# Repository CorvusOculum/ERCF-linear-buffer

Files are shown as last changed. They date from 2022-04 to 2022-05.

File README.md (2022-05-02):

# ERCF-linear-buffer

NOTE: This is a work in progress.

This is a filament buffer system designed to replace the "caged loops" style of buffer that is popular, such as the Enraged Rabbit Carrot Patch.  This buffer differs from caged loops in that the filament is pushed down a very long linear channel as a single loop.  The narrow, yet wide channel prevents the filament from twisting.  When a particular channel is in use, the filament is retracted out of the channel and only contacts half of the pulley leading to very little drag in the system.  The channels are cut from 3/8 inch thick foam board.

I designed this system as a low drag alternative to the Carrot Patch style of buffer which can in my own experience be problematice with very long reverse-bowden lengths.  With a looping system, you add loops to add distance to the buffer.  When you add four or five loops, the drag can be quite significant.  This system only ever has a half loop of the pulley and when more length is needed, you simply use longer channels.  

# BOM

(N refers to the number of channels in your MMU system) 

    xN - Buffer Channel Pulley Block
    
    xN - Buffer Channel Top Block
    
    xN - Buffer Channel Pulley
    
    xN - Buffer Channel Pulley Axel
    
    xN - Buffer Channel Bottom Block
    
    xN - Buffer Channel Desiccant Tray
    
    xN - 608 RS "Skateboard" Bearing
         NOTE: I personally remove the seals with a sharp tool, and 
         then use a cleaner such as break cleaner to completely remove 
         all grease from the bearing.  The pulleys should spin like a
         fidget spinner when completed.  I don't know if this helps 
         anything at all...  But I do it anyway...
    
    2 x N / 3 - Buffer Channel Brace Bracket
         NOTE: You will want a 2 braces per channel to support the 
         foam board and mount the buffers to whatever you'll be using. 
         So in a 9 channel MMU system you will want: 2*9/3= 6 Brackets. 
    
    xN - M3 x 35mm SHCS
    xN - M3 Heatset Inserts
    
    28 x N - 6mm x 3mm disc magnets 
          NOTE: Depending on the quality of your magnets you may be able
          to use fewer.  The parts are designed to accomodate a lot of 
          magnets on the assumption that you will be using cheap ones from
          AliExpress or Amazon.  If you have genuine N52's for example, far
          fewer will be required.  Experiment.
    
    2 x N - PC4-M10 Straight through Pneumatic Fitting
	      NOTE: MUST BE A THROUGH FITTING!

# Printing

While I printed mine in ABS with the standard Voron recomended profile, you could certainly dial down infill and perimeters and still be fine...  The buffers will not experience very much if any mechanical stress.  

# Construction

Your foam board should be cut using calipers.  Measure the inside of the narrow side of the channel and lock the calipers off.  Then use the calipers to score the foamboad.  Cut carefully with a long metal straightedge.  Do both short sides first, then measure the inside with of the long edge between the two smaller foam board pieces and cut the wider sides.  You want to have the edges of the short side foam board in the corners and not the long sides.  This is important!  The length of these channels should be roughly half the the length of your reverse bowden, but it is wise to add 10%-15% extra just in case.  Usually the foamboard will friction fit and stay in place, however it's a good idea to glue them.

Even with the drag reduction from this system, it is still critically important that you not have any sharp corners in your bowden tubing.  Large graceful bends are your friend!  

It is also highly recommended that you use 2.5mm or 3mm inner diameter (4mm outer) PTFE tubing everywhere per the recommendation of @Ette the creator of the ERCF.

# Credits
The pulley used in this design was taken from the EnragedRabbitProject by Ette.  This was by design, as anyone who has built an ERCP and has issues like I had can reuse the part when they switch.
https://github.com/EtteGit/EnragedRabbitProject

Inspiration for this style of buffer was also taken from the TodWuff's Linear Buffer Project.  I actually would have made this buffer rather than designing my own, but the cable channel they used was backordered in Canada by several months.
https://github.com/TodWulff/-MHz-ERCF-Filament-Rack-Buffer-Tube-Assy

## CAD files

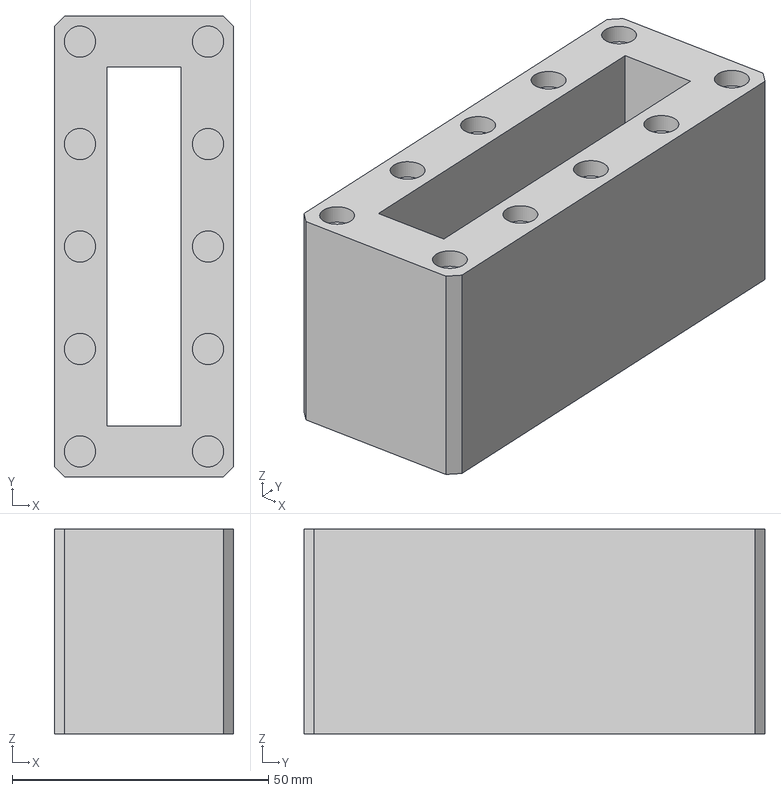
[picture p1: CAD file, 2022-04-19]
CAD/buffer_channel_top_block.step
35.0 x 90.0 x 40.0 mm

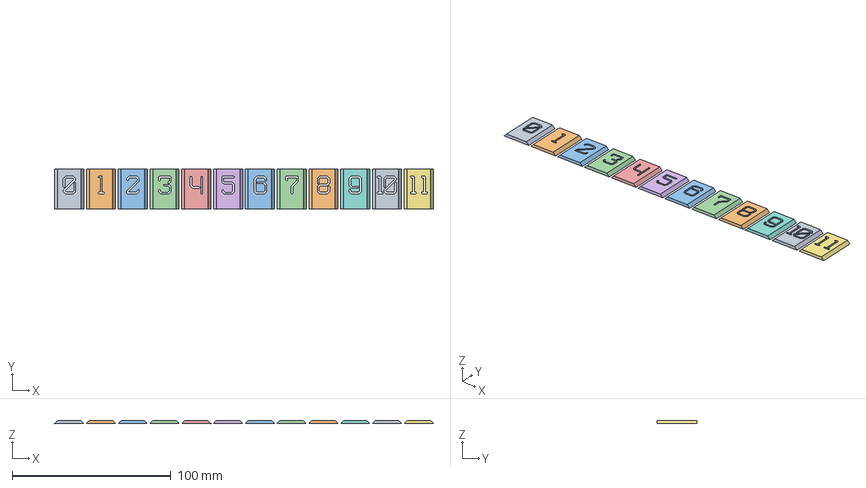
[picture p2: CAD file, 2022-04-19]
CAD/buffer_channel_number_plates.step
238.5 x 25.0 x 1.93 mm

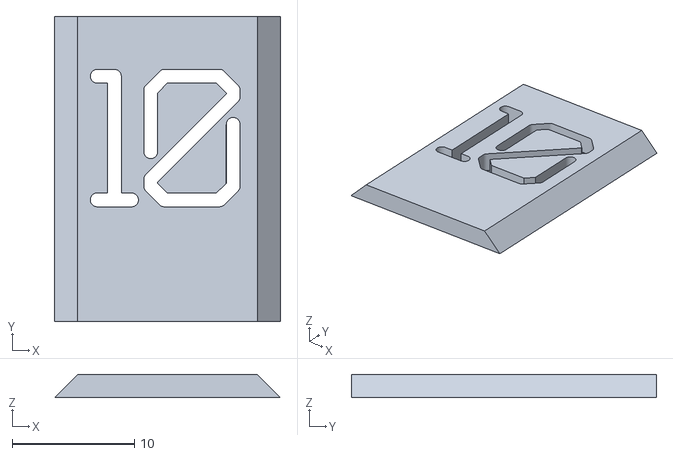
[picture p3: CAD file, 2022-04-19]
STL/{a}_buffer_channel_number_plate_10_x1.stl
18.5 x 25.0 x 1.90

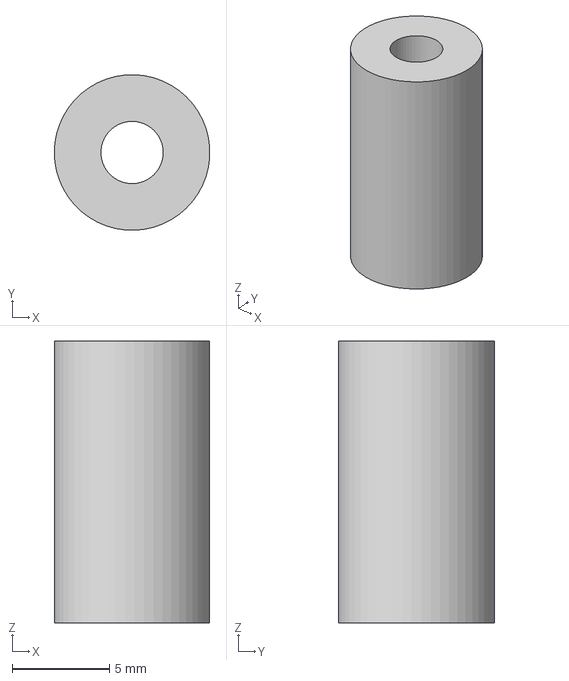
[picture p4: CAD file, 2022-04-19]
CAD/buffer_channel_pulley_axel.step
7.99 x 8.00 x 14.5 mm

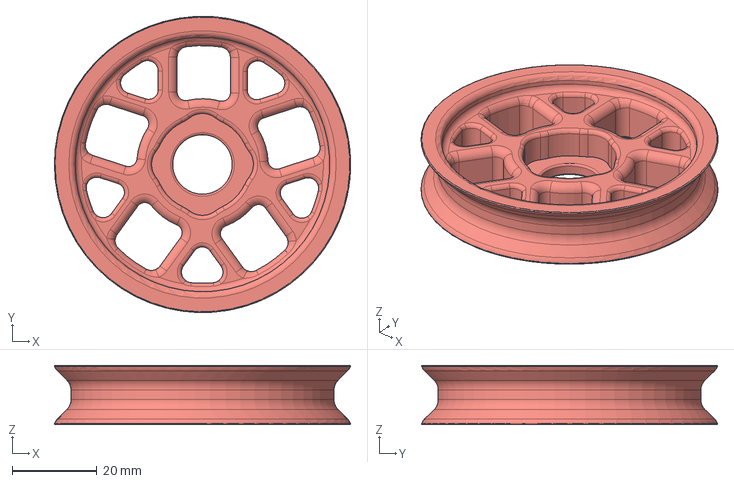
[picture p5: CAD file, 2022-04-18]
CAD/buffer_channel_pulley.step
69.8 x 69.8 x 14.0 mm

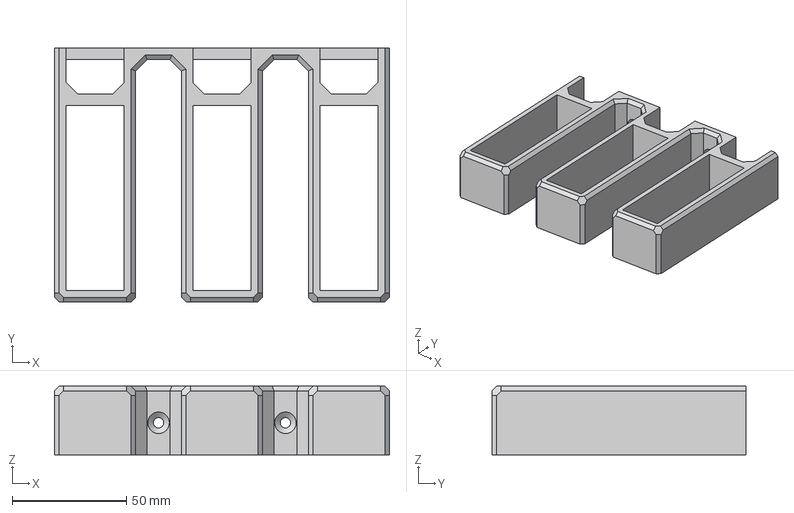
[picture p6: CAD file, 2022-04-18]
CAD/buffer_channel_brace_bracket.step
146.5 x 111.0 x 30.0 mm

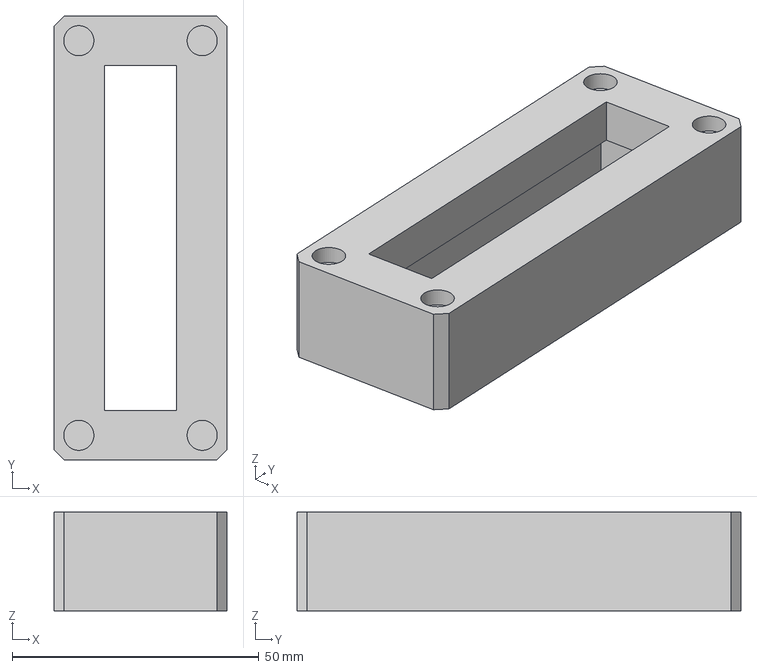
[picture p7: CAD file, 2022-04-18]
CAD/buffer_channel_bottom_block.step
35.0 x 90.0 x 20.0 mm

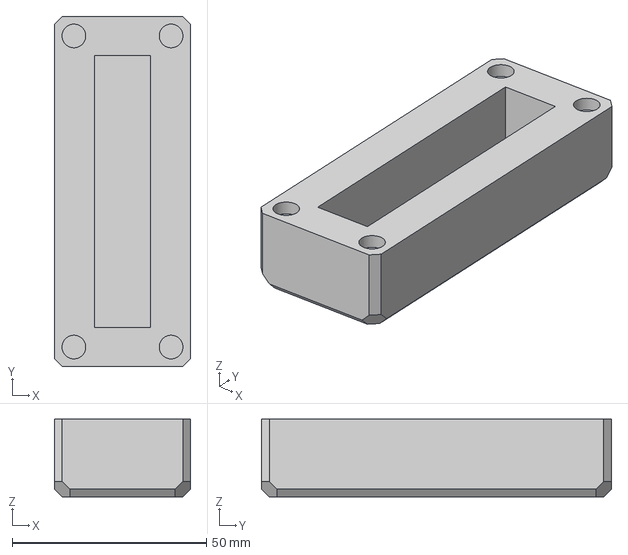
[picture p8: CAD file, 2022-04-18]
CAD/buffer_channel_desiccant_tray.step
35.0 x 90.0 x 20.0 mm

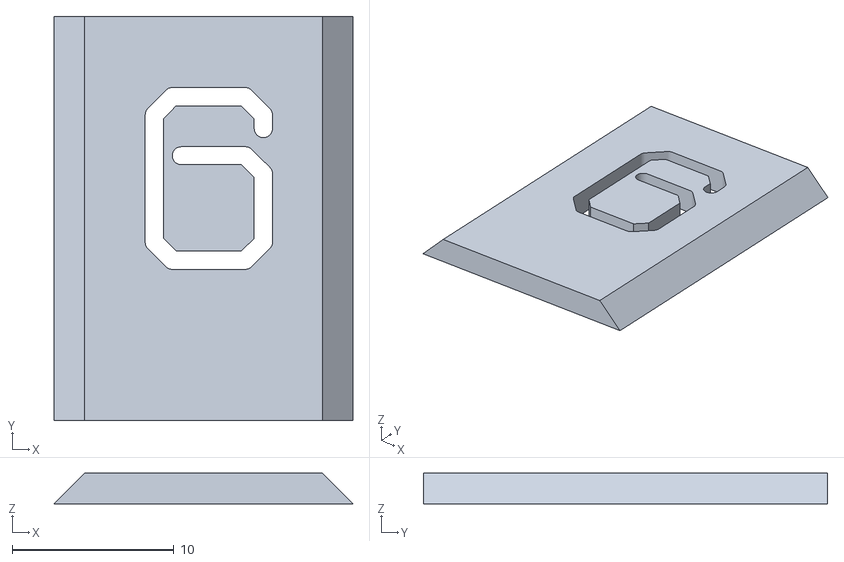
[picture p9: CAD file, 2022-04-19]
STL/{a}_buffer_channel_number_plate_6_x1.stl
18.5 x 25.0 x 1.90

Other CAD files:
STL/buffer_channel_top_block_xN.stl
STL/{a}_buffer_channel_number_plate_11_x1.stl
STL/{a}_buffer_channel_number_plate_1_x1.stl
CAD/buffer_channel_pulley_block.step
STL/{a}_buffer_channel_number_plate_2_x1.stl
STL/{a}_buffer_channel_number_plate_0_x1.stl
STL/{a}_buffer_channel_number_plate_3_x1.stl
STL/{a}_buffer_channel_number_plate_4_x1.stl
STL/{a}_buffer_channel_number_plate_7_x1.stl
STL/buffer_channel_bottom_block_xN.stl
STL/buffer_channel_brace_bracket_xNdiv3.stl
STL/buffer_channel_desiccant_tray_xN.stl
STL/buffer_channel_pulley_axel_xN.stl
STL/buffer_channel_pulley_block_xN.stl
STL/buffer_channel_pulley_xN.stl
STL/{a}_buffer_channel_number_plate_5_x1.stl
STL/{a}_buffer_channel_number_plate_8_x1.stl
STL/{a}_buffer_channel_number_plate_9_x1.stl

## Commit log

2022-04-19 Update buffer_channel_pulley_block_xN.stl
    Added detail to the threaded holes for the PC4-M10 connectors to help the slicing process with bridging.
    [buffer_channel_pulley_block_xN.stl]
2022-04-19 Update buffer_channel_pulley_axel_xN.stl
    Minor size increase to fit bearing more snugly.
    [buffer_channel_pulley_axel_xN.stl]
2022-04-19 Reduced depth of one extrusion to remove small chance of filament catching
    [buffer_channel_top_block.step, buffer_channel_top_block_xN.stl]
